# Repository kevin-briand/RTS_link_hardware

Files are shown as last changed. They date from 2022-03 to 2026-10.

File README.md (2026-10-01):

# RTS Link Hardware

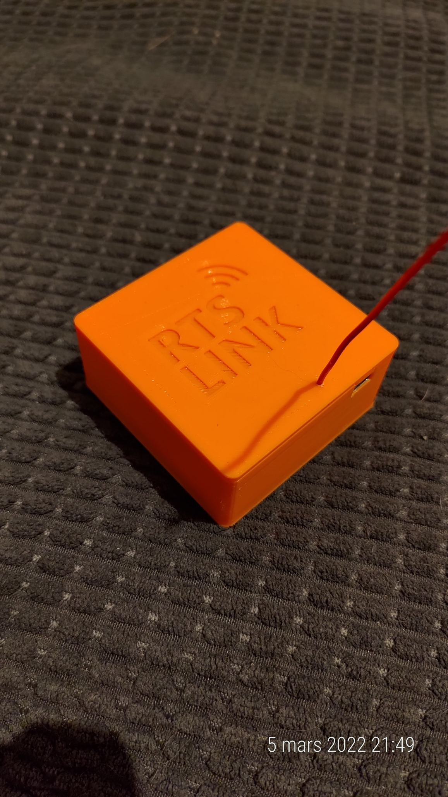
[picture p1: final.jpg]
RTS Link transmitter


USB transmitter for [RTS Link](https://github.com/kevin-briand/rts_link), the Home Assistant integration that controls Somfy RTS covers.

Based on the [SomfyRTS library](https://github.com/etimou/SomfyRTS) (Etienne Mouragnon, GPL v3), included in `rts_link/` with a few fixes.

## Bill of materials

- Arduino Nano (ATmega328P)
- RFM69HW radio module
- Level shifter 5 V ↔ 3.3 V (the RFM69 is a 3.3 V part)
- Antenna: a quarter-wave wire of about **17.3 cm** soldered on the ANT pin
- PCB (`PCB/`, DipTrace) and 3D printed case (`3D Print/`: box, lid, optional DIN rail support and lock)

## Wiring

Pins used by the firmware (through the level shifter):

| RFM69HW | Arduino Nano |
|---|---|
| NSS | D10 |
| MOSI | D11 |
| MISO | D12 |
| SCK | D13 |
| DIO2 (data) | D3 |
| 3.3 V / GND | 3.3 V / GND |

## Flashing the firmware

1. Open `rts_link/rts_link.ino` with the Arduino IDE, board **Arduino Nano** (ATmega328P).
2. Check the settings at the top of the file:
   - `#define DRY_RUN` must stay **commented out**, otherwise nothing is emitted on the radio.
   - `myRTS.setHighPower(true);` must stay **enabled** in `setup()`: the RFM69HW cannot emit without it.
3. Upload with a **regular USB upload**.
   - Do **not** use *Upload using programmer*: it erases the whole chip, including the EEPROM where the rolling codes are stored, and every cover would have to be paired again.
   - A regular upload keeps the EEPROM: paired covers keep working after a firmware update.

> On Linux, if the upload fails with `Permission denied` on `/dev/ttyUSB0`, add your user to the `dialout` group (`sudo usermod -aG dialout $USER`) and log in again.

> Close the sketch in the Arduino IDE and reopen it after pulling new files: an IDE left open may save its old copy over them.

## Checking the transmitter

Open the serial monitor at **115200 baud**, line ending **Newline**. At startup the transmitter prints:

```
Somfy RTS link
```

If `RADIO ERROR` is printed on the next line, the RFM69 does not answer: check the wiring and the 3.3 V supply. The other commands keep answering, but nothing is emitted.

Close the serial monitor before plugging the transmitter into Home Assistant: both programs would read the same port.

## Serial protocol

One command per line, terminated by `\n`, at 115200 baud.

| Command | Action | Answer |
|---|---|---|
| `PROG` | Creates a new virtual remote and sends its PROG frame | ID of the new remote |
| `MULTIPROG;<id>` | Sends a PROG frame with an existing remote (pair one more cover) | `<id>` |
| `UP;<id>` / `DOWN;<id>` / `STOP;<id>` | Sends the command with remote `<id>` | `OK` |
| `PING` | Checks that the transmitter answers | `OK` |
| `RESET` | **Factory reset**: forgets every remote and its rolling code. Every cover must be paired again | `OK` |
| anything else, unknown or invalid ID | — | `ERROR` |

Notes:
- Up to 255 remotes. The next free ID is stored in the last EEPROM byte, rolling codes use 2 bytes per remote from address 0.
- At least 1 s of silence is kept between two radio emissions (`MIN_GAP_MS`), so grouped commands are sent one cover after the other.

## Usage

1. Plug the transmitter into the Home Assistant host.
2. Install the [RTS Link integration](https://github.com/kevin-briand/rts_link) and select the transmitter USB port.
3. Pair your covers from the RTS Link panel.

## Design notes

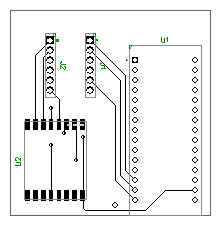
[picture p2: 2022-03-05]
PCB/Top.png

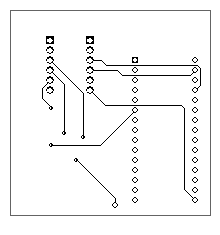
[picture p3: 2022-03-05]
PCB/Bottom.png

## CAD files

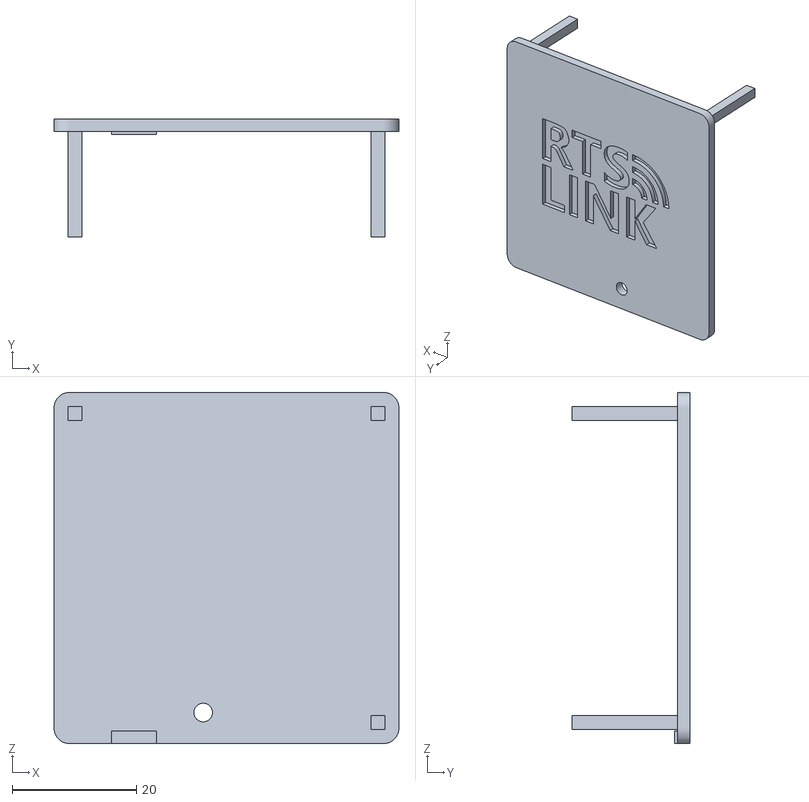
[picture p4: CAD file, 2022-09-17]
3D Print/couvercle.stl
55.5 x 19.0 x 56.5

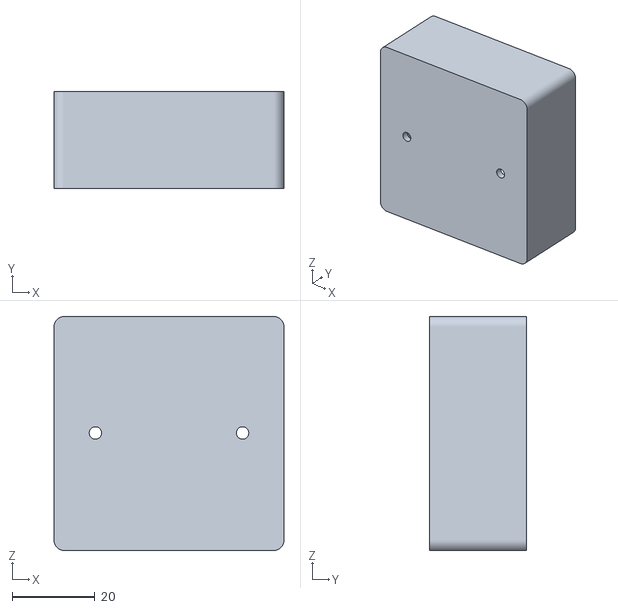
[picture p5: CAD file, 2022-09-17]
3D Print/boite.stl
55.5 x 23.5 x 56.5

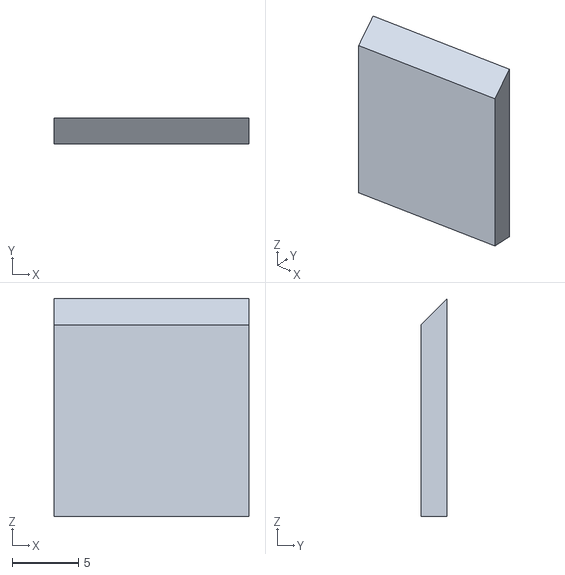
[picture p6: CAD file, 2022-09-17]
3D Print/Verrou DIN.stl
14.8 x 2.00 x 16.5

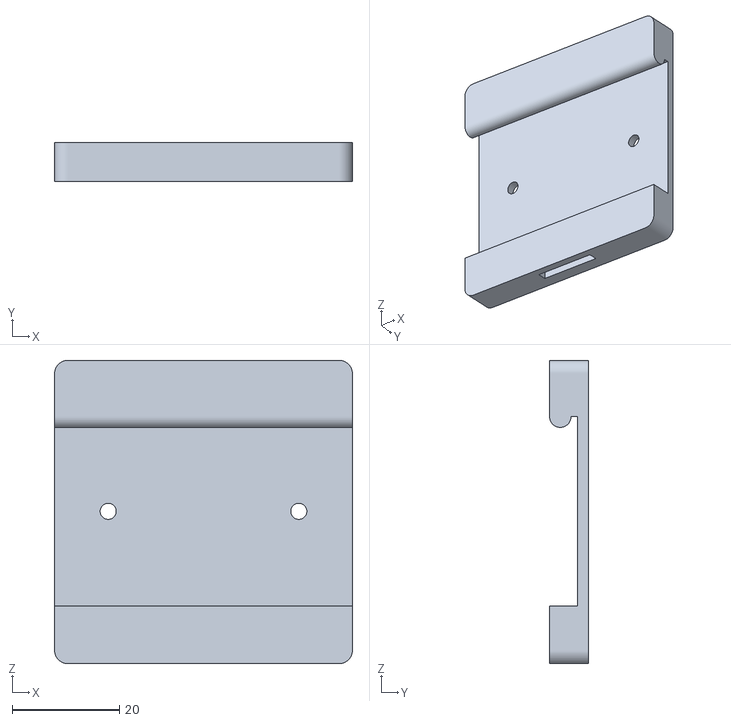
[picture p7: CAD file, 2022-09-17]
3D Print/Support DIN.stl
55.5 x 7.25 x 56.5

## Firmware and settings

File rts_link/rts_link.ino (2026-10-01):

#include "SomfyRTS.h"
#include <EEPROM.h>

// Serial protocol (one command per line, terminated by '\n'):
//   PROG            -> allocates a new virtual remote, sends PROG, answers "<id>"
//   MULTIPROG;<id>  -> sends PROG with an existing remote, answers "<id>"
//   UP;<id> / DOWN;<id> / STOP;<id> -> answers "OK"
//   PING            -> answers "OK"
//   RESET           -> factory reset: clears ALL remotes AND their rolling codes,
//                      every paired cover must be paired again. Answers "OK"
// Any invalid command answers "ERROR".

// Uncomment to test the serial protocol without emitting anything on the radio
// #define DRY_RUN

SomfyRTS myRTS(3, TSR_RFM69); //Tx pin number, transmitter type
                              //pin number : pin connected to the transmitter DATA pin or to the DIO2 pin on RFM69
                              //transmitter type can be TSR_RFM69 or TSR_AM (for a generic AM 433.42MHZ transmitter)

// The next free remote id is stored in the last EEPROM byte.
// Rolling codes use 2 bytes per remote from address 0, so ids must stay below MAX_COVERS.
const int ID_ADDRESS = EEPROM.length() - 1;
const int MAX_COVERS = 255;
int idCover = 0;

// Somfy motors need a silence between two transmissions, otherwise
// back-to-back commands (grouped actions in HA) are ignored.
const unsigned long MIN_GAP_MS = 300;
unsigned long lastEmission = 0;

void sendRadio(int id, byte cmd) {
#ifndef DRY_RUN
  unsigned long elapsed = millis() - lastEmission;
  if (lastEmission != 0 && elapsed < MIN_GAP_MS) delay(MIN_GAP_MS - elapsed);
  myRTS.sendSomfy(id, cmd);
  lastEmission = millis();
#endif
}

// Parses the id after ';'. Returns -1 if missing, not a number, or not allocated yet.
int parseId(const String &value) {
  int sep = value.indexOf(';');
  if (sep == -1) return -1;
  String idStr = value.substring(sep + 1);
  if (idStr.length() == 0) return -1;
  for (unsigned int i = 0; i < idStr.length(); i++) {
    if (!isDigit(idStr[i])) return -1;
  }
  int id = idStr.toInt();
  if (id < 0 || id >= idCover) return -1;
  return id;
}

void reply(const String &msg) {
  Serial.print(msg);
  Serial.print('\n');
}

void setup() {
  Serial.begin(115200);
  Serial.setTimeout(100); // only used if a line arrives without '\n'

  bool radioOk = myRTS.initRadio();
  myRTS.setHighPower(true); //have to call it after initialize for RFM69HW

  idCover = EEPROM.read(ID_ADDRESS);
  if (idCover >= MAX_COVERS) idCover = 0; // erased/corrupted EEPROM reads 0xFF

  reply("Somfy RTS link");
  if (!radioOk) reply("RADIO ERROR"); // RFM69 not answering: check wiring/power
}

void loop() {
  if (!Serial.available()) return;

  String value = Serial.readStringUntil('\n');
  value.trim();
  if (value.length() == 0) return;

  String cmdName = value;
  int sep = value.indexOf(';');
  if (sep != -1) cmdName = value.substring(0, sep);

  if (cmdName == "PROG") { // Add a new cover
    if (idCover >= MAX_COVERS) {
      reply("ERROR");
      return;
    }
    int id = idCover;
    sendRadio(id, PROG);
    idCover++;
    EEPROM.update(ID_ADDRESS, idCover);
    reply(String(id));
  }
  else if (cmdName == "MULTIPROG") { // Pair one more cover with an existing remote
    int id = parseId(value);
    if (id == -1) {
      reply("ERROR");
      return;
    }
    sendRadio(id, PROG);
    reply(String(id));
  }
  else if (cmdName == "UP" || cmdName == "DOWN" || cmdName == "STOP") {
    int id = parseId(value);
    if (id == -1) {
      reply("ERROR");
      return;
    }
    byte cmd = STOP;
    if (cmdName == "UP") cmd = UP;
    else if (cmdName == "DOWN") cmd = DOWN;
    sendRadio(id, cmd);
    reply("OK");
  }
  else if (cmdName == "PING") {
    reply("OK");
  }
  else if (cmdName == "RESET") { // Factory reset, see header
    for (unsigned int i = 0; i < EEPROM.length(); i++) {
      EEPROM.update(i, 0);
    }
    idCover = 0;
    reply("OK");
  }
  else {
    reply("ERROR");
  }
}

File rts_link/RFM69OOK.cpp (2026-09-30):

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
// Licence can be viewed at
// http://www.gnu.org/licenses/gpl-3.0.txt
//
// Please maintain this license information along with authorship
// and copyright notices in any redistribution of this code
// **********************************************************************************
#include "RFM69OOK.h"
#include "RFM69OOKregisters.h"
#include <SPI.h>

volatile byte RFM69OOK::_mode;  // current transceiver state
volatile int RFM69OOK::RSSI; 	// most accurate RSSI during reception (closest to the reception)
RFM69OOK* RFM69OOK::selfPointer;

bool RFM69OOK::initialize()
{
  const byte CONFIG[][2] =
  {
    /* 0x01 */ { REG_OPMODE, RF_OPMODE_SEQUENCER_OFF | RF_OPMODE_LISTEN_OFF | RF_OPMODE_STANDBY },
    /* 0x02 */ { REG_DATAMODUL, RF_DATAMODUL_DATAMODE_CONTINUOUSNOBSYNC | RF_DATAMODUL_MODULATIONTYPE_OOK | RF_DATAMODUL_MODULATIONSHAPING_00 }, // no shaping
    /* 0x03 */ { REG_BITRATEMSB, 0x03}, // bitrate: 32768 Hz
    /* 0x04 */ { REG_BITRATELSB, 0xD1},
    /* 0x19 */ { REG_RXBW, RF_RXBW_DCCFREQ_010 | RF_RXBW_MANT_24 | RF_RXBW_EXP_4}, // BW: 10.4 kHz
    /* 0x1B */ { REG_OOKPEAK, RF_OOKPEAK_THRESHTYPE_PEAK | RF_OOKPEAK_PEAKTHRESHSTEP_000 | RF_OOKPEAK_PEAKTHRESHDEC_000 },
    /* 0x1D */ { REG_OOKFIX, 6 }, // Fixed threshold value (in dB) in the OOK demodulator
    /* 0x29 */ { REG_RSSITHRESH, 140 }, // RSSI threshold in dBm = -(REG_RSSITHRESH / 2)
    /* 0x6F */ { REG_TESTDAGC, RF_DAGC_IMPROVED_LOWBETA0 }, // run DAGC continuously in RX mode, recommended default for AfcLowBetaOn=0
    {255, 0}
  };

  pinMode(_slaveSelectPin, OUTPUT);
  SPI.begin();

  for (byte i = 0; CONFIG[i][0] != 255; i++)
    writeReg(CONFIG[i][0], CONFIG[i][1]);

  setHighPower(_isRFM69HW); // called regardless if it's a RFM69W or RFM69HW
  setMode(RF69OOK_MODE_STANDBY);
  // Wait for ModeReady, give up if the radio does not answer (wiring, power...)
  unsigned long start = millis();
  while ((readReg(REG_IRQFLAGS1) & RF_IRQFLAGS1_MODEREADY) == 0x00) {
    if (millis() - start > 100) return false;
  }

  selfPointer = this;
  return true;
}

// Poll for OOK signal
bool RFM69OOK::poll()
{
  return digitalRead(_interruptPin);
}

// Send a 1 or 0 signal in OOK mode
void RFM69OOK::send(bool signal)
{
  digitalWrite(_interruptPin, signal);
}

// Turn the radio into transmission mode
void RFM69OOK::transmitBegin()
{
  setMode(RF69OOK_MODE_TX);
  detachInterrupt(_interruptNum); // not needed in TX mode
  pinMode(_interruptPin, OUTPUT);
}

// Turn the radio back to standby
void RFM69OOK::transmitEnd()
{
  pinMode(_interruptPin, INPUT);
  setMode(RF69OOK_MODE_STANDBY);
}

// Turn the radio into OOK listening mode
void RFM69OOK::receiveBegin()
{
  pinMode(_interruptPin, INPUT);
  attachInterrupt(_interruptNum, RFM69OOK::isr0, CHANGE); // generate interrupts in RX mode
  setMode(RF69OOK_MODE_RX);
}

// Turn the radio back to standby
void RFM69OOK::receiveEnd()
{
  setMode(RF69OOK_MODE_STANDBY);
  detachInterrupt(_interruptNum); // make sure there're no surprises
}

// Handle pin change interrupts in OOK mode
void RFM69OOK::interruptHandler()
{
  if (userInterrupt != NULL) (*userInterrupt)();
}

// Set a user interrupt for all transfer methods in receive mode
// call with NULL to disable the user interrupt handler
void RFM69OOK::attachUserInterrupt(void (*function)())
{
  userInterrupt = function;
}

// return the frequency (in Hz)
uint32_t RFM69OOK::getFrequency()
{
  return RF69OOK_FSTEP * (((uint32_t)readReg(REG_FRFMSB)<<16) + ((uint16_t)readReg(REG_FRFMID)<<8) + readReg(REG_FRFLSB));
}

// Set literal frequency using floating point MHz value
void RFM69OOK::setFrequencyMHz(float f)
{
  setFrequency(f * 1000000);
}

// set the frequency (in Hz)
void RFM69OOK::setFrequency(uint32_t freqHz)
{
  // TODO: p38 hopping sequence may need to be followed in some cases
  freqHz /= RF69OOK_FSTEP; // divide down by FSTEP to get FRF
  writeReg(REG_FRFMSB, freqHz >> 16);
  writeReg(REG_FRFMID, freqHz >> 8);
  writeReg(REG_FRFLSB, freqHz);
}

// Set bitrate
void RFM69OOK::setBitrate(uint32_t bitrate)
{
  bitrate = 32000000 / bitrate; // 32M = XCO freq.
  writeReg(REG_BITRATEMSB, bitrate >> 8);
  writeReg(REG_BITRATELSB, bitrate);
}

// set OOK bandwidth
void RFM69OOK::setBandwidth(uint8_t bw)
{
  writeReg(REG_RXBW, readReg(REG_RXBW) & 0xE0 | bw);
}

// set RSSI threshold
void RFM69OOK::setRSSIThreshold(int8_t rssi)
{
  writeReg(REG_RSSITHRESH, (-rssi << 1));
}

// set OOK fixed threshold
void RFM69OOK::setFixedThreshold(uint8_t threshold)
{
  writeReg(REG_OOKFIX, threshold);
}

// set sensitivity boost in REG_TESTLNA
// see: http://www.sevenwatt.com/main/rfm69-ook-dagc-sensitivity-boost-and-modulation-index
void RFM69OOK::setSensitivityBoost(uint8_t value)
{
  writeReg(REG_TESTLNA, value);
}

void RFM69OOK::setMode(byte newMode)
{
    if (newMode == _mode) return;

    switch (newMode) {
        case RF69OOK_MODE_TX:
            writeReg(REG_OPMODE, (readReg(REG_OPMODE) & 0xE3) | RF_OPMODE_TRANSMITTER);
      if (_isRFM69HW) setHighPowerRegs(true);
            break;
        case RF69OOK_MODE_RX:
            writeReg(REG_OPMODE, (readReg(REG_OPMODE) & 0xE3) | RF_OPMODE_RECEIVER);
      if (_isRFM69HW) setHighPowerRegs(false);
            break;
        case RF69OOK_MODE_SYNTH:
            writeReg(REG_OPMODE, (readReg(REG_OPMODE) & 0xE3) | RF_OPMODE_SYNTHESIZER);
            break;
        case RF69OOK_MODE_STANDBY:
            writeReg(REG_OPMODE, (readReg(REG_OPMODE) & 0xE3) | RF_OPMODE_STANDBY);
            break;
        case RF69OOK_MODE_SLEEP:
            writeReg(REG_OPMODE, (readReg(REG_OPMODE) & 0xE3) | RF_OPMODE_SLEEP);
            break;
        default: return;
    }

    // waiting for mode ready is necessary when going from sleep because the FIFO may not be immediately available from previous mode
    while (_mode == RF69OOK_MODE_SLEEP && (readReg(REG_IRQFLAGS1) & RF_IRQFLAGS1_MODEREADY) == 0x00); // Wait for ModeReady

    _mode = newMode;
}

void RFM69OOK::sleep() {
  setMode(RF69OOK_MODE_SLEEP);
}

// set output power: 0=min, 31=max
// this results in a "weaker" transmitted signal, and directly results in a lower RSSI at the receiver
void RFM69OOK::setPowerLevel(byte powerLevel)
{
  _powerLevel = powerLevel;
  writeReg(REG_PALEVEL, (readReg(REG_PALEVEL) & 0xE0) | (_powerLevel > 31 ? 31 : _powerLevel));
}

void RFM69OOK::isr0() { selfPointer->interruptHandler(); }

int8_t RFM69OOK::readRSSI(bool forceTrigger) {
  if (forceTrigger)
  {
    // RSSI trigger not needed if DAGC is in continuous mode
    writeReg(REG_RSSICONFIG, RF_RSSI_START);
    while ((readReg(REG_RSSICONFIG) & RF_RSSI_DONE) == 0x00); // Wait for RSSI_Ready
  }
  return -(readReg(REG_RSSIVALUE) >> 1);
}

byte RFM69OOK::readReg(byte addr)
{
  select();
  SPI.transfer(addr & 0x7F);
  byte regval = SPI.transfer(0);
  unselect();
  return regval;
}

void RFM69OOK::writeReg(byte addr, byte value)
{
  select();
  SPI.transfer(addr | 0x80);
  SPI.transfer(value);
  unselect();
}
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

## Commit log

2022-03-05 Adding PCB + 3D Print
    [boite RTS.stl, couvercle RTS.stl]
2022-09-17 Adding DIN support
    [Support DIN.stl, Verrou DIN.stl, boite.stl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]

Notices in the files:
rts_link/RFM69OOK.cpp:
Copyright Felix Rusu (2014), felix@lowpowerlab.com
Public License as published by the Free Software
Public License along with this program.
